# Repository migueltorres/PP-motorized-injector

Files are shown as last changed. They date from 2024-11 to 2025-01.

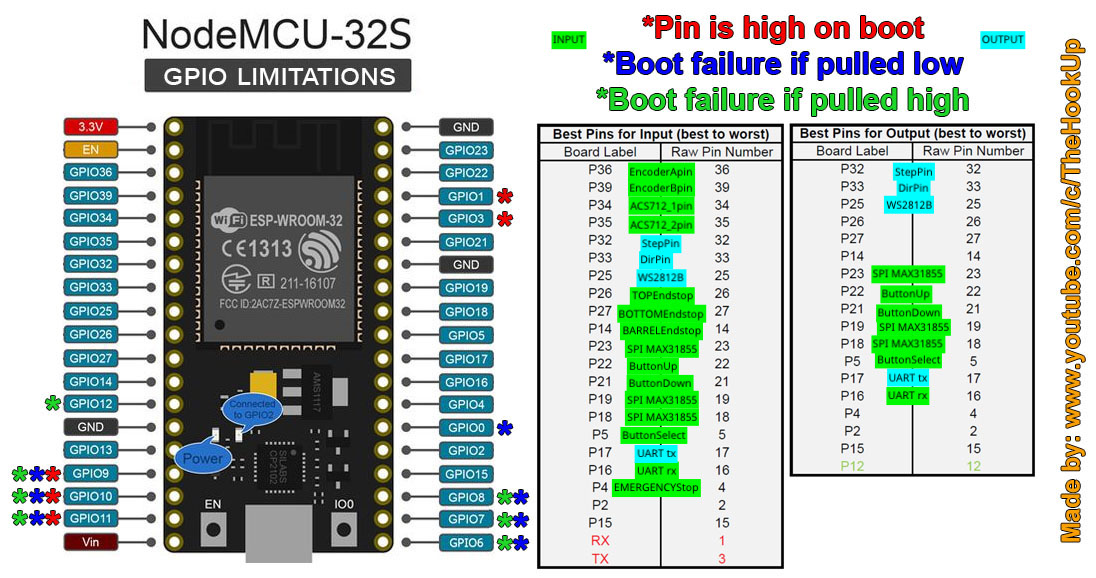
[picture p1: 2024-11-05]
GPIO_Limitations_ESP32_NodeMCU.jpg

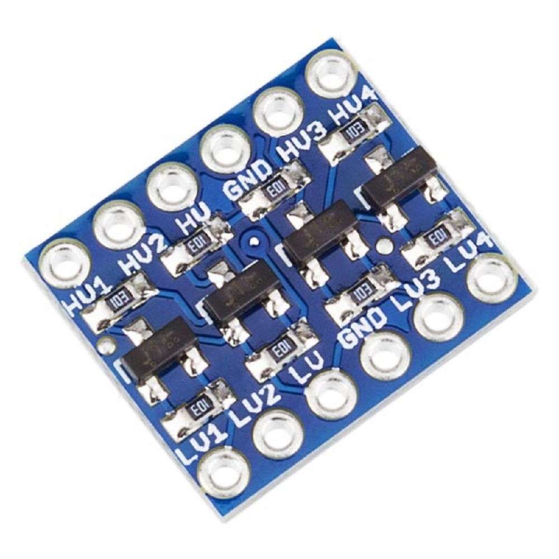
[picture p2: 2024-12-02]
4 channel bidirectional LLC.jpg

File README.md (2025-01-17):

# PP-motorized-injector
Motorized plastic injector using Arduino code to be open sourced with Precious Plastic initiative once working!

I create this (1st time on Github!) repo as I would like help in getting this finished and resolving issues that I am having (please excuse the extension of the descripcion, I am not known for my ability to summerize!):

I am making a PP influenced style injector, but controlled with Arduino to be able to send a Nema 34 160mm with Encoder, with 1:20 reduction to a 26mm ID / 50cm stroke injection barrel with control enough to be able to inject up to a 1/10th of a cm3 of plastic (more or less, the actual system is capable of even btter precision, but plastic is a dynamic fluid so don't expect the practice to reflect the theory 100%).. this need came about because the manual arbour version I made is so powerful that it injects great into large thick 3D moulds, but is difficult to fill smaller 2D moulds made from 8mm sandwich (originally these were a good format for the first lever-operated PP injector), as it is too easy to overfill and get flash, and then is very difficult to open the 2D mould and the part is ruined,.. and the smaller the part to inject, the more difficult it is to "feel" when it is full and to tehn over-fill - this machine should be able to calibrate to each mould the exact amount and speed of injection to get a perfect fill each time 🤞

I have done the mechanical design (still open to a couple of last minute choices about things like how to detect the presence of the mould/ nozzle blocking mech/ barrel blocking mech, etc) and believe it to be quite solid, as I have designed a few machines myself (https://bazar.preciousplastic.com/andys-recycling-machines/), including an arbour injector before the PP version came out.. I had asked for help documenting this to open source the design as this is a weak point for me, but didn't get much response 🤷, hopefully this time can get the help I need on the software side.. this is supposed to be open sourced as well..  

the machine for me should be able to inject into any type of mould, up to a maximum size (the space under the nozzle), and volumen (supposedly about 265cm3, pratice this will be about 200cm3 as the cold flakes have air), and different size moulds basically have a wooden block under them to make up the space needed so they are all at the same height, so to speak...  I generally inject max about 50-60cm3 with the manual machine, which has slightly smaller volumen (about 180cm3) and Refill after each injection

I have so far managed to integrate (inductive) endstops for top and bottom plunger movement, a barrel slip detection (my method on my manual injector of stopping heat from passing from the barrel to the rest of the machine, and so to be more efficient, is to clamp the barrel between 2 offset clamps, and the space is filled with cork sheet, works very well and the clamps do not get hot, but if the machine is incorrectly used and the plunger forced with nothing underneath the barrel, happens with the manual version too, then the barrel can clip in the clamp, changing the space below/calibration of the injection process), temp in nozzle detection (low temp, no move), and a 3 button LED backlit keypad at the height of the Nozzle to aid use of the machine when working down there (purging, zeroing for injection, injection itself, colores change and functions of each button)... all running on a ESP32 exclusively dedicated to running the motor, encoder, endstops, etc.

The other half of the electronics is a 2nd ESP32 Touchscreen display, connected to the motor ESP32 via UART, where can graphically add mould profiles, change parameters, store and load a list of moulds, and also graphically show the contents of the barrel; how much time each Refill has been in the barrel (during Production with the manual injector, I Refill after each Injection, but have to give time for each Refill Block to heat up as it travels down the barrel, so it has had time enough to reach melt temp before being injected, otherwie get a cold injection), once calibrated with a minTime can advise that the NextInjection amount and the RefillBlock at present about to be injected both pass in TimeHeated and amount to inject, to make sure that it will not be too cold.. everything is stored on this Display in flash, and only the NextInjection parameters are sent to the motor ESP32 via UART...  these are mould variables that change with each mould, there are also a load more common machine variables that are changeable from the display, like offsets from endstops, speeds and amounts of a compression function with auto-detection of max compression (the Nema will skip, the Encoder Compare function will notice this and reduce/stop compression), which once set up will rarely have to be changed/tuned

So far I have checked that each electronic component works with simple separate test sketches directly to the motor ESP.. the Display ESP I am still in the GUI design stage, using EEZ Studio (first time too, so learning curve 😜), but eventually will have to be connected, but until this 2nd stage is done, the same serial info should be able to be sent via Serial to change mould parameters, then all workings of the machine, following a State Machine programming style, will be possible from the 3 keypad control, as each State will give different options to the buttons to proceed or go back to other States as needed...

Here in this repo I have uploaded all notes, design considerations, and so far a few captures of the machine, and my next steps I hope to generate interest on the Discord server (which also rarely use😬).. I am 52 years old, completely self-learnt in all I have ever been interested in since I left home at 15 years old, so am very aware that what I do know is out-weighed by what I don't know in most of what I am learnt in life.. I am level 1 autistic, but intelligent enough to have masked most of my life until I auto-diagnosed about 6-7 years ago.. I personally do not like social networks, but aim to use Discord to learn from others and help try and get this machine up and running ASAP.. I have tried using ChatGPT with varing levels of success in getting every more complex sketches working (tab separated sketches seem to be my limit, can't seem to get more than the most basic ones working, when I understand that need to have a more modular approach with more tab separated header files, but here is were I have reached my limit!), but am also self-employed and PP here in Tenerife is not big enough to be able to dedicate all of my time, so I have other professional obligations that take time away from this proyect 🤷

I am not entirely sure about how to best proceed in questions of organisation via Discord, how to better use Github to centralize development of this proyect to benefit everyone in PP with this machine that I hope will open up easy injection to more people, but after seeing the latest video about PP problems and need to get to v5, I would like to make this public/ open source now (have been working over a year on this, on and off, and have the alpha built and waiting for a working sketch!)

I would need help integrating the State Machine I have designed into a working sketch, capable of responding to user button presses, and updating the ActualMould struct via Serial monitor to be able to change easier the MouldVariables (instead of having to reflash each time), and finalizing the way of detection for Compresion (nozzle blocking), Purging (barrel blocking but nozzle open, small forces to purge and check that plastic is ready for injection), and Injection (same, but now using the full force for the programed move to fill the mould).. am contemplating now placing Strain gauges below the injection platform (will see how much strain is registable as I made this area pretty solid to be able to resist the injection pressure, about 1500kgs estimated), and/or Time of Flight distance sensors next to the nozzle to "see" that there is something that should block the barrel, and considering intergrating a couple of current sensors in one of the Nema motor pairs (SimpleFOC style, but my driver (for this hardware version) is "step/dir", so cannot use SimpleFOC) to detect peaks (or lack of) motor current that may help me indicate build up of pressure that could show there is / is not something below the barrel..

Please revise the contents of the repo, advise on what else is needed here, info to understand better the machine/concept, etc, and if someone on Discord could help maybe make a thread/channel (I think it is called that..?) to organise and separate interest on advancing this proyect, that would be a big help too...

google sheets (exported from Numbers 😬) of BoM, calcs, and particularly the State Machine.. although can't remember when did this export..
https://docs.google.com/spreadsheets/d/1dTpOeWWeW3WKA8ZfMgRmvt531EJANU4MFCuCA3LTdP0/edit?usp=sharing

Thanks in advance, I feel I am a pretty good mechanic, my "tok" is getting machines to work (my manual machines work pretty well), but software, although have a few years unfer the belt am learning and can follow quite well in ArduinoIDE (PlatformIO is still a bit more of a mistery for me, hace tried and not got good results yet..), getting a more complex sketch like this to integrate is driving me a little crazy!

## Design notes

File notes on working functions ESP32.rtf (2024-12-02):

CHECK VOLTAGES THRU ACTUAL CIRCUIT, LLC, ETC
With ONLY step/dir connected from ESP32 to LLC, Dir(LLC)&Gnd (ESP32)=3,3v, but Dir(LLC)&Gnd (distribution board on backboard)=2v (or less?), and OUTPUT Dir was even less..?? 1.4-1.6v
alberto has given me 2 types of 4 channel LLC, one bidirectional, the other directional, so can try these, however will need 2x 5v and 3.3v wiring to power said LLCs, as need 2 of them…
** FIXED ** after Alberto recommended testing with a pot in series with first Dir signal and then Pulse signal, discovered that DRIVER inputs logic HIGH/LOW threshold is 1.3v, so NO LLC needed

Encoder 🟢

ESP32Encoder simpleEncoderDemo works fine, 1000PPR, via 3.3v, and pins spec in sketch.. in theory is via PCNT hardware counter… so do NOT need to update any variable, just when sending encoder position data, include a call to the counter for the actual value… this will almost always be in a static moment, so no need to call constantly, but during moves, can call each 0.5-1s..?
Encoder colours wires:
Red - vcc
White - gnd
Yellow - A+
Blue - B+
CHECKS! test how many encoder steps are 100% stroke, and use this variable (maxEncoderStepsPlunger) as a check before each InjectProcess starts, to make sure enough material is left in machine (before Purge show on screen, at PurgeZero also check and show Green or Red on screen if NextInject (+ 5%?) fits or not
CHECKS! during testing phases, include a Home function that does NOT automatically zero encoder, just reports EncoderPosition, to see if steps have been lost after a few hours use

FastAccelStepper 🟡
revise course https://valarsystems.com/blogs/val-2000/section-10-motor-setup as they use this library, ESP32, and show how to dedicate 1 Core of ESP32 to ONLY motor functions (core 0 is por default dedicated to wifi, and loop() is core 1, so as no wifi, use core 0), to guarantee uninterrupted function on this core, all other MCU loads cargo on other core, Encoder calls are off both cores and callable when required

include actual button/pot sketch to check functionality on ESP32…. does not respond to button presses, butpot values do work.. had also included both new inline ACS712 current sensors (with inline 10k resistor)..
separate and test each component with example sketches…
FIXED! it seems driver logic HIGH/LOW threshold is 1.3v, so NO LLC needed (tried 3 types LLC, all gave strange voltages at driver input on connecting to driver 🤷)
🟡 working 2 button sketch with fixed speed 50%, w/o LLC, motor moves smooth and with acceleration on button presses (Constant move).. to incorporate, distinct Programmed and Constant motor move functions

MotorFunction should be called from StateMachine, a) first taking the variables pertinent to that state and writing them to global standard MotorFunction variables, b) call MotorFunction to move motor with its standard variables, which should move as per the variables just updated

As will assign motor function as a task to Core 0, have to verify that calls from Core 1 loop() to this task/function on Core 0 will not need any special extra coding..?

WS2812B_tests 🟢
working test sketch to change colores of LEDs behind buttons
🔵 brightness of ALL LED’s change on button press, could be acceptable so user sees any brightness change is SOME button has been pressed
🟡 currentDuration tests not quite working, to change color of other LED’s after 1s, ok, but other LED does not change back to original color on release/!isPressed/changed/rose etc, not sure how to do this.. revise more examples..? adding another .update before second “if” does work, but not always..? also, is possibly adding more MCU time to check button, + debounce time..?
Also, in my use case, a button hold for currrentDuration will (in all cases?) make a change of State Machine, where a new set of color instructions will be generated anyway..? Will not need to change colores back (not working well), only reduce brightness (working fine) before next State will change colours anyway

Buttons_tests 🟢
Blue wire - down
Orange wire - up
orange/white wire - select
blue/white - gnd
respond perfectly well with Bounce2 library, can also measure a delay, si WB2812B tests above, check that all “long presses” will make a State Change anyway

Inductive endstops_tests
will be assigning as buttons with Bounce2 library as well, as they are basically buttons with HIGH/LOW logic…
Top & Bottom sensors are NO, 5v, go to LOW / GND on activation, so pins with pull-up to avoid floating
Clamp sensor is NC, 0v, goes HIGH / 5v on activation, so pin with pull-down to avoid floating
min working voltage 5v (do not work at 3.3v), and min signal returned 4.4 top and bottom, 4.7 clamp 🔽 step-down/ LLC

StateMachine - revise spreadsheet made to indicate all situations

INIT States, on power on
INIT_HEATING // temp of machine too low to allow movement
⁃ power on, temp < 170C,
⁃ NO MOTOR MOVE POSSIBLE,
⁃ button LED's RED solid

INIT_HOT_NOT_HOMED // temp above min, ready for movement
⁃ temp > 170C
⁃ button LED's YELLOW solid

INIT_HOMED_ENCODER_ZEROED // Homed for FIRST time after power on Zeros Encoder, ALL later homings do NOT reset Encoder
⁃ user has pressed for first time Home
⁃ motor moves to TopEndStop
⁃ Encoder is zeroed, InitEncoderZeroedFlag =1
⁃ Motor is only zeroed when about to do measured moves, will move to Refill position (set position from TopEndStop)

REFILL & COMPRESSION states
REFILL // position with plunger just above barrel opening, so user can load cold plastic into machine
⁃ motor moves to RefillOffsetPositiion
⁃ button LEDs GREEN/OFF/OFF (will return to Refill after NextInjection) or GREEN/BLUE/BLUE (will NOT return to Refill after NextInjection, EndOfDayFlag=1)
⁃ user can press both lower buttons to change bool EndOfDayFlag
⁃ user can press GREEN button to confirm loading complete & NozzleBlack is in place

COMPRESSION // motor will move down first at med speed, until ComparisonFunction goes above threshold, then will continue until 0 speed
⁃ button LED's RED (Cancel) / OFF (nothing) / RED FLASHING (Starting Compression), YELLOW FLASHING (ComparisonFunction active), GREEN SOLID (completed)
⁃ ComparisonFunction compares SentMotorSteps and RealEncoderSteps for every, ej. 20 (?) steps.. when detects ej 50% (?) loss (only 10 steps Real to Sent), reduces Speed to 50% (?) and continues again, until Speed is below minSpeedThresholdForCompression, and then exits function
⁃ InsufficientFillCheck - if Encoder steps show that < 80-90% (?) of stroke is full (motor moved > 20-10% (?) of StrokeLength before ComparisonFunction finishes, then advices user that another Refill is required and goes back to Refill

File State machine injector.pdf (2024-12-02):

ReadyToInject… buttons change to green top and bottom,
middle yellow
🟢 🟡 🟢 ☑ 🔼 🔽 ….

Power
on

INIT_HEATING

(external
control)

INIT_HOT_NOT
_HOMED

Temp

>170˚C

Request user to

HOME machine,
press 🟡 🔼 (2s)

INIT states, check temps ALWAYS, maybe give option to HOME at another point, to test if ENCODER has lost steps

Request user to
CONFIRM REFILL

barrel & position
barrel block

INSUFFICIENT_
FILL

COMPRESSION
detected less
than 80-90%
stroke is full?

REFILL & COMPRESSION states

!EndOfDayFlag
marked?
🌑 🌑 /🔵 🔵
Once machine is ready, hot, | and encoder Initially homed,
automatically goes to Refill | position and awaits user input

Once Compression is completed to sufficient level, and contents has been heated long enough (millis timer for each batch of Refilled plastic..?)

EndOfDayFlag

Injection Process

User positions mould | & blocks with platform
confirms Proceed with | double green button press
!EndOfDayFlag | ! EndOfDayFlag ?
MACHINE_EMPTY | Power off

INIT_HOMED_E
NCODER_ZER
OED

REFILL

Injection Process uses ActualInjectParams and CommonInjectParams, automatic, only CANCEL button or EMERGENCY STOP

INJECTION | HOLD_INJECTI
ON | RELEASE

COMPRESSIO
N

ProgrammedMotorMove function: parameters set from State to appropriate variable for appropriate move

ContinousMotorMove function: either from user button press (Purge), or internal command variable (Compress until motor & encoder desync steps)

🛑 🛑 🛑 ☑ 🔼 🔽
(no movement possible)

🟡 🟡 🟡 ☑ 🔼 🔽 (not homed yet, no refill/injection can be performed yet)

(🟢 🌑 🌑 ☑ 🔼 🔽 , waiting confirm Refill 🌑 🌑 !EndOfDayFlag 🔵 🔵 EndOfDayFlag cancel process ☑ 🛑 , middle off 🌑 🔼 , bottom button flashes red 🔽 🔴 , change to flashes yellow 🔽 🟡 , then green solid 🔽 🟢 , and complete

pressing both green buttons 🟢 🟢 ☑ 🔽 for 2s enters Injection Process

Press both bottom buttons 2s to change from black (!EndDay) to Blue (EndDay, no more Refills) or visa versa

User PURGES
plastic using UP /

DOWN buttons until
presses green to ZERO
PURGE_ZERO | ANTIDRIP

buttons change to green top, yellow bottom pair) 🟢 🟡 🟡 ☑ 🔼 🔽

green bottom pair 🟢 🟢 🔼 🔽 , press top 2s to cancel injection, bottom pair together 2s after positioning mould to start injection cycle

red top 🛑 ☑ (cancel
injection)go back to
ReadyToInject

pressing middle yellow button 🟡 🔼 can take back to Refill position (only way to get there once EndOfDayFlag is marked),

INJECT_TO_MOULD
red top (cancel), green bottom pair 🛑 🟢 🟢 ☑ 🔼 🔽

Communications via UART:
During certain States, the STM32 will be listening for commands to change to other States, or to change ActualInjectParams, or CommonInjectParams... this will only happen during States that make sense, for example ReadyToInject, Refill, NOT during motorMoves

however, the STM32 will be transmitting every 1s to the ESP32 the actual Encoder position, the actual Nozzle temp, which the ESP32 display will later show a graphic rep of the barrel and the contents as rectangles, with either timers in each rectangle, or colours to show plastic melt stage... other good Encoder transmission points may be at the end of Refill/ Compression functions, as these will be the boundary between rectangular blocks representing plastic Refills and therefore melt stages

Also, on listening and receiving Params changes (for Common or Actual InjectParams, the STM32, after updating these variables, will transmit back to the Display so they can be shown on screen and compared to requested data

STOPS:
EMERGENCY STOP, if pressed, immediate stop of actual function. if function is NOT plunger down move (compression or injection), then releasing E-STOP will return to same point, if IS down move, then will immediately de Release Function, and then enter Purge Function so plunger can be moved manually

Endstops:
TopEndStop: when plunger reaches Top of stroke, the barrel is supposedly empty, so simply stop any more movement up (possible send plunger to Refill position, as is a nearby offset, or only allow move down*)

BottomEndStop: the encoder data should update the total stroke of plunger and add the NextActualInjectionParams to the actual plunger position, and advise if the injection can be completed or not, but if the BES is triggered without this warning, stop motor move, only allow motor move up*

Barrel Endstop: if the barrel has been detected as having moved from its fixed place, then stop any movement/ injection and advise with error, only allow up move to allow release of pressure so clamp can be inspected without pressure*

* in theory, in none of these cases coincide with a user button config that ALLOWS any movement anyway, so possibly could include this movement ONLY... also, these types of endstops errors can easily be indicated by flashing LEDs red in order:- if top endstop is triggered, flash goes up, bottom, flashing goes down, if barrel, centre and exterior alternate 🤔

Buttons input and output:
Lower keypad consists of 3 buttons, select, up & down, with LEDs behind, that change use as per the State of the machine and user input required to operate. Simple direct connection GPIO with Pullup is considered enough.

Barrel & Nozzle block detection however is still complicated, as the force experimented in this area (full downforce from Nema motor via 20:1 reductor, about 1500kg estimated min) makes use of traditional mechanical endstops very difficult, and proximity sensores also may not fully verify that a decent blocking mech is in place, contacting both against the platform and against the barrel / nozzle edge (as per compression or purge) - it is considered a L-shaped 30x3mm profile with a blind end, as used with the manual machine, together with a toggle mech to be able to invert this L-profile as per need of the moment, manually... for an electronic check, this pivoting and inverting mech would have to be electrically isolated from the rest of the machine (which experiments continuity throughout the frame so is impossible to know when one part of the frame touches another, as there is already an alternative conductive route for the signal)

A plastic sleeve isolating the fixed side of a hinge and the mobile side that carries the L-profile mech could be a way to later connect said profile to a pin, but it would activate on touching EITHER barrel/nozzle OR platform base, when what is really needed is to assure the profile is correctly positioned between both sides, not just that is contacting either of them

For the moment, can only think about a Manually Display User Reminder to place the L-profile in the correctly orientated position as per the Purge or Compression function that need to be realised...

The same goes for the presence of the mould itself, complicated by the fact that each mould, although metallic, have a wooden base to supplement the height differences between moulds and the full injection space

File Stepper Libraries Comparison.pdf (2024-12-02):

### Feuille1

### Page 1

| Acceleration | Max steps/sec | Units | Non-blocking methods | ISR Note 1 | Notes
Stepper | No | ? | Step RPM | Blocking | No | Easy to use, only three methods
AccelStepper | Yes | 4000 Step | | Both | No
MobaTools | Yes (start/stop ramps) | ? | Step Degree (angle) | Non-blocking | No | The MobaTools are a compilation of classes that are useful in the model railway environment (but not only there). It can control servos and stepper motors (and other things).
FlexyStepper | Yes | 7000 | Step Revolution mm | Both | No
SpeedyStepper | Yes | 12500 | Step Revolution mm | Both | No | Similar to FlexyStepper but optimized for speed Cannot modify target position, speed or acceleration while motor is moving
FastAccelStepper | Yes | 50,000 to 200,000 depending on processor | Hz (steps/s) mHz (steps/1000s) microsec/step ticks | Both | Yes | Fully interrupt/task driven - no periodic function to be called from application loop Not all GPIO pins are allowed on ATmega architectures, see documentation
ESP_FlexyStepper | Yes | ? | Step Revolution mm | Both | Yes | This library is used to control one or more stepper motors with a ESP 32 module. Based on S.Reifels FlexyStepper library.
TeensyStep | Yes | 300,000 | Step | Both | Yes | Compatible with Teensy 3.x boards The library is able to handle synchronized as well as independent movement of up to 4 groups of up to 10 motors
TeensyStep4 | Yes | ? | Step | Both | Yes | Compatible with Teensy 4.x boards This library is very experimental and no support can be given at the moment

Note 1 : ISR (Interrupt Service Routine) is for librairies that can run as interrupt tasks without the need to use a periodic function in the main loop(). With this feature, one can do whatever is needed in the main loop() without having to worry about the impact on the motors.

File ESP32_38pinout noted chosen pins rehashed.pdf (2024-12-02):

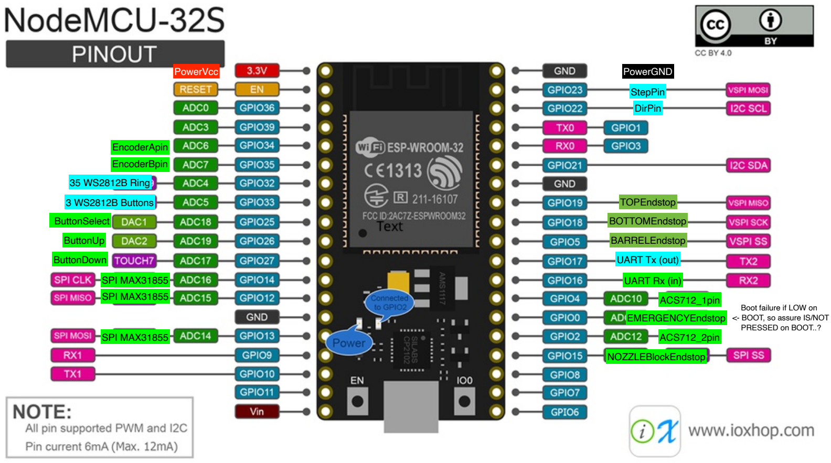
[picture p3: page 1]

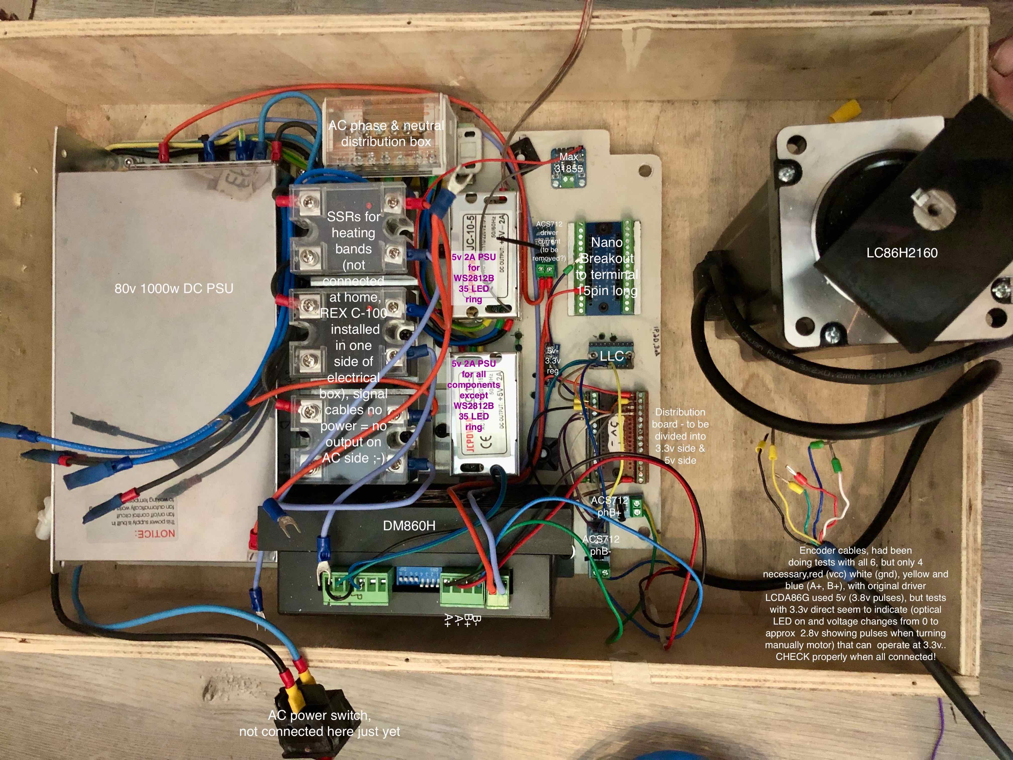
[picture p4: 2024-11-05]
electrical backboard layout.jpeg

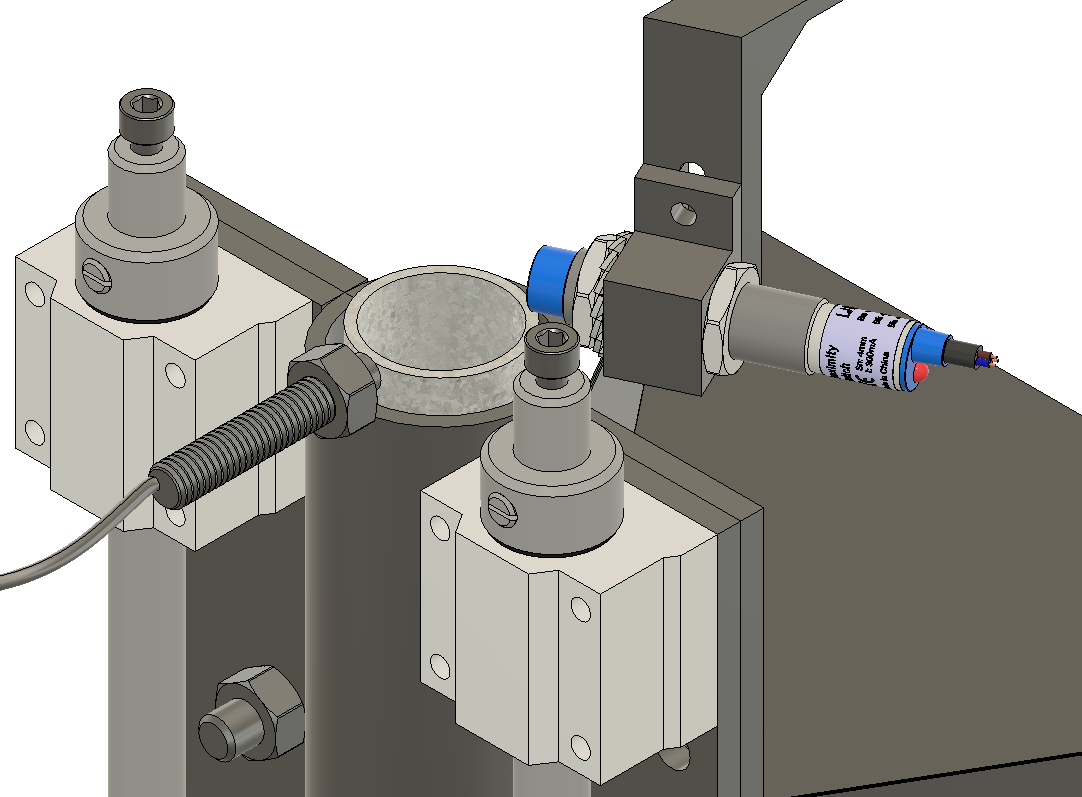
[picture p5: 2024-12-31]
fotos machine/clsoe up barrel slip, and bottom endstop.png

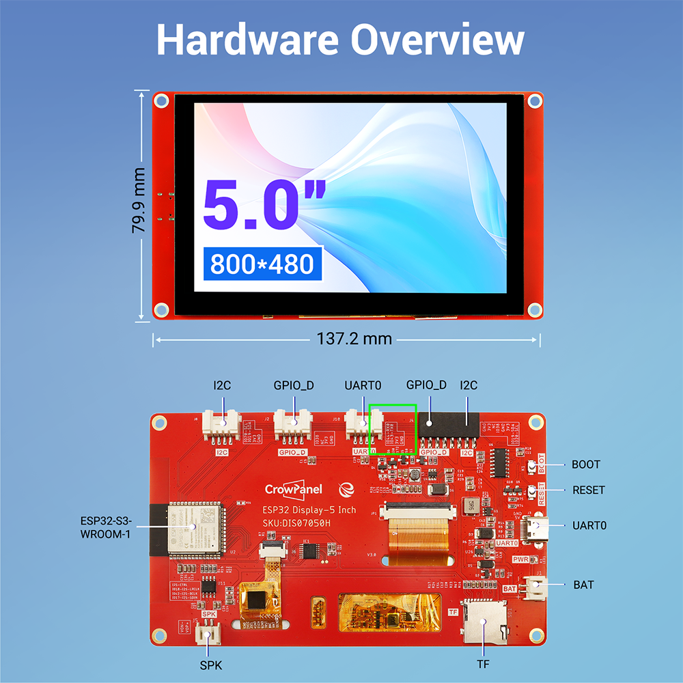
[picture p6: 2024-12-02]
elecrow 5 RGB 800x480 touch display/5-DIS07050H-SCH_PCB/dimension_size_of_ESP32_5inch_HMI_display.png

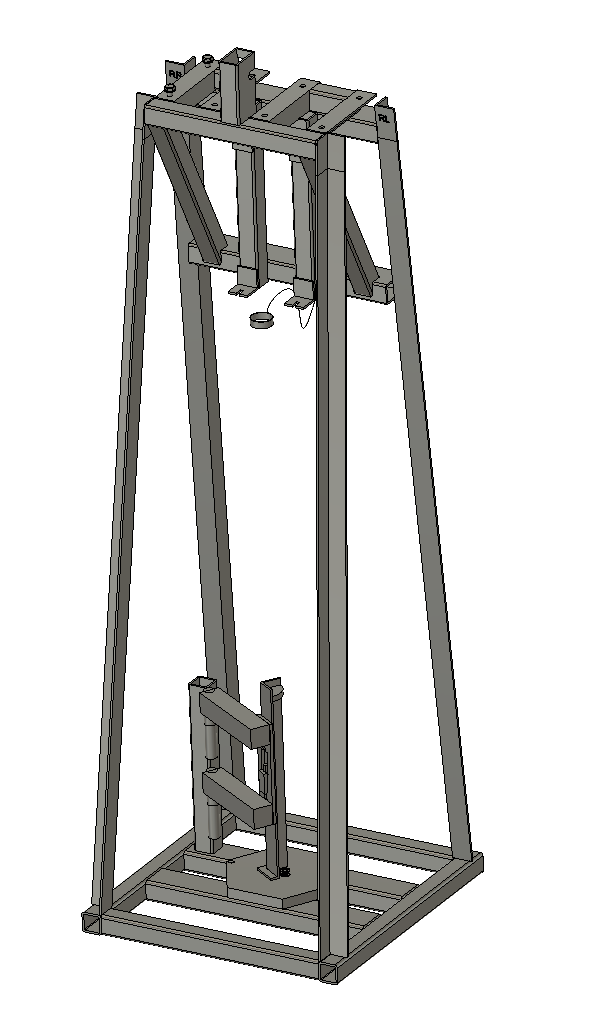
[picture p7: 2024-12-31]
fotos machine/frame only.png

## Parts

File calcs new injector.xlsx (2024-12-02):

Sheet: Calcs - Pump & injection pressu
Pump & injection pressures
Concepto |  |  | example
Dia embolo/cm | 2.600 |  | 4.500
Area embolo/cm2 | 5.309 |  | 15.904
Paso movimiento embolo/cm | 50.0 |  | 50.000
Volumen util/cm3 | 265.465 |  | 795.216
volume/s injection speed/cm3/s | 25
Tamaño orificio inyección/cm | 0.550 |  | 0.500
Area orificio/cm2 | 0.238 |  | 0.196
 |  | circumference | rev/full shot
Spur gear D1/mm | 60 | 188.4955592 | 2.652582385
radius/m | 0.030 |  | rev gear/25cm3 shot
power motor/Nm | 12.0 |  | 0.2498056796
power on spur gear/N | 400.000 |  | length of piston move/mm
power on spur gear/kg | 40.789 |  | 47.08726127
Nema 34 rpm | 900 | rps | 15
 |  |  | reduce from 15rps to 0.2498rps (shot 25cm3/s)
mechanical advantage gained from reducer/kg: | 2449.358 | ideal reducer by: (NOT actually used, just a nice calc!) | 60.05
Nm | 24020.000 |  | 🔼 after adding calcs for spur & shaft, this value seriously passes max values for both spur teeth and shaft torsion, so reduced majorly
pressure embolo en/ kg/cm2 | 461.334
punta embolo | 2449.358

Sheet: Calcs - Parts
Parts
part | code | price |  | value | unit
Nema34 closed loop stepper | https://robotdigg.com/product/1228/Two-phase-NEMA34-closed-loop-stepper-motor SS86P2156 | 120 | shaft 14mm 12Nm holding torque approx 900rpm=15rps | 12 | Nm
driver | https://www.robotdigg.com/product/1229 | included above..?
REDUCTOR RSTV050 TAMAÑO MOTOR 71 EJE DE ENTRADA 14 MM ratio i:20 would seem max for this setup | https://www.zuendo.com/corona-sin-fin/5166-reductor-rstv050-tamano-motor-71-eje-de-entrada-14-mm.html | 97.02 | ratio i:20 | 20 | :1 ratio
 |  |  | output after reductor | 240 | Nm
EJE SIMPLE DE SALIDA PARA REDUCTOR RSTV50 25 mm | https://www.zuendo.com/accesorios-para-reductores/3110-eje-simple-de-salida-para-reductor-todos-los-tamanos.html | 17.6 | diameter shaft | 0.025 | m
Spur gear mod 2.5, D1 60, hardened teeth | 22401-0125250024 | 34.32 | 60mm D1 14mm D2 | 0.03 | radius / m
 |  |  | power from spur gear onto gear rack | 8000 | N/radius spur
Gear rack 25 OD, mod 2.5 | 22425-025150X1000 | 130.67
Tube ID 26 OD 30 | 29050-0130X1000 | 20.64 | power from spur gear onto gear rack | 815.8 | kg
 |  |  | pressure/cm2 plunger PUMP PRESSURE | 153.7 | kg/cm2 / bar
 |  |  | pressure/cm2 nozzle hole INJECTION PRESSURE | 3433.634398 | kg/cm2 / bar
max rev Nema/ rps | 5 | rps | 25cm3 shot ratio to full shot | 10.61858317 | :1 ratio
steps/s | 2000 |  | rev/spur full shot | 2.652582385 | full = 50cm
rpm | 300 | rpm | time for full shot | 10.61032954 | s
rev Nema AFTER reductor /rps | 0.25 | rps | circumference spur | 18.84955592 | cm
rpm gear | 15 | rpm | steps / circ spur / cml | 8000 | 424.4131816
pulse/rev Nema // gear | 400 | 8000 | cm3/ cir spur | 100.08 | cm3
max pulse = rps / gear rps | 2000 | 0.25 | cm circ spur/s | 4.71238898 | cm
encoder pulses/ rev Nema | 2000
encoder pulses / max rps | 10000
25cm3 = cml / steps | 4.708726127 | 1998.445437 | cm3/ s | 25.01944716 | cm3
1cm3 = cml /steps | 0.188 | 79.93781747 | rev gear/25cm3 shot | 0.250 | rev
1cm lineal embolo = vol cm3 / steps | 5.309 | 424.4131816 | s/25cm3 shot | 0.999 | s
50cm linear plunger heated zone/ plastic full stroke = vol cm3/ steps | 265.4645792 | 21220.65908
67cm linear plunger full range move to topendstop 50cm stroke + 2cm cold + 6cm opening + 16cm clamp - 7cm plunger tip |  | 28435.68317 | 3819.718634 | <- RefillOffset steps= 16cm clamp - 7cm plunger tip x steps/cml sum of lengths to topendstop -> | 67
heated full stroke offset from topendstop,-> and from refill —> |  | 7215.024 | 3395.305

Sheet: Calcs - Volumes
Volumes
Injection Volumen = pi*radius^2*stroke | ej1, buscar volumen | ej2 buscar paso
EJEMPLOS de Calculos SOLO
Dia embolo / cm | 2.6 | 4.2
Paso embolo / cm | 50 | 10.82686688
Volumen inyectado /cm3 | 265.4645792 | 150

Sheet: Calcs - Rack & pinion, vertical
Rack & pinion, vertical
concept |  | Tangential force on rack | Torque on pinion |  | max calculated for heat hardened steel gear teeth
moved mass / kg | m | 4 |  |  | S=400Pa, w=25mm
gravitational constant / m/s2 | g | 9.81 |  |  | mod 2.5, 60mm Dp
coefficient of friction / u | u | -
maximum acceleration / m/s2 | a | 0.25 |  | max load N | 8225
pressing Force due to application / N | Fe | 8000 |  |  | with 50:1 reduction, about 1/2 the expected 😬
 |  |  |  |  | with 20:1 reduction, about 3% SF over the expected 🧐😰
Force on Rack / N | Fr | 8040.24
Torque on pinion / Nm |  |  | 241.2072
 |  |  |  |  | https://www.engineersedge.com/calculators/gear-tooth-strength-calculator.htm

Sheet: Calcs - Shaft calcs on chosen o
Shaft calcs on chosen output shaft
Shear stress on solid shaft | t = Tr/J | for 25mm OD | angular deflection | a=L*T/(J*G) | for Iron 63 GaP Shear modulus
 | Mpa | 78.22783763 |  | degrees | 0.8708128448
shear stress / t | Pa | 78227837.63 | angular shaft deflection / a | radians | 0.01519855131
twisting moment / T | Nm | 240 | length of shaft / L | m | 0.153
radius from center to stressed surface / r | m | 0.0125 |  |  | 🔼 length of shaft “as-theoretical-held-at-1-end”, whilst in reality, the reductor holds along 93mm of total 153mm, so torsion possibly only on last 53mm? = 0.3 degrees 🧐
polar moment of inertia of area / J | m4 | 3.83495197e-08 | Shear modulus of rigidity / G | Pa | 63000000000
J = (pi*Dˆ4/32) |  | 3.83495197e-08 |  |  | 🔼 as per Zuendo, axle is Iron, not steel!

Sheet: Calcs - Shaft calcs on motor sh
Shaft calcs on motor shaft, 14mm
Shear stress on solid shaft | t = Tr/J | for 14mm OD | angular deflection | a=L*T/(J*G) | for steel 75 GaP Shear modulus
 | Mpa | 22.27241186 |  | degrees | 0.4788470367
shear stress / t | Pa | 22272411.86 | angular shaft deflection / a | radians | 0.008357457403
twisting moment / T | Nm | 12 | length of shaft / L | m | 0.197
radius from center to stressed surface / r | m | 0.007 | Shear modulus of rigidity / G | Pa | 75000000000
polar moment of inertia of area / J | m4 | 3.771481981e-09
J = (pi*Dˆ4/32) |  | 3.771481981e-09

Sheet: BoM - Plunger parts
Plunger parts
part | description | web | reference | price (sin IGIC) | price € (con IGIC) | units | subtotal
Nema34 closed loop stepper | shaft 14mm 12Nm holding torque approx 900rpm=15rps | https://robotdigg.com/product/1228/Two-phase-NEMA34-closed-loop-stepper-motor SS86P2156 | CL86H2156 | $75.00 | €76.25 | 1 | €76.25
driver |  | https://www.robotdigg.com/product/1285/DM542,-DM556-or-DM860H-stepper-motor-driver | DM860HJK | $29.00 | €29.48 | 1 | €29.48
 |  | https://www.robotdigg.com/product/976/80VDC-7.2A-DSP-Stepper-Motor-Driver |  | $42.00 | €42.70 |  | €0.00
PSU 80v DC for Nema |  | https://www.robotdigg.com/product/1564/60V-or-80V-DC-output-500W-or-1000W-power-supply | S-1000-80 | $80.00 | €81.34 | 1 | €81.34
REDUCTOR RSTV050 TAMAÑO MOTOR 71 EJE DE ENTRADA 14 MM ratio i:20 would seem max for this setup | ratio i:20 | https://www.zuendo.com/corona-sin-fin/5166-reductor-rstv050-tamano-motor-71-eje-de-entrada-14-mm.html | B14, i=20..? could go to i:30 if decide that Nema is not reaching top speed with actual i:20, but this means more torque, and certain mechanical calcs indicate overload of gear teeth or axle 😬 | €80.17 | €85.78 | 1 | €85.78
EJE SIMPLE DE SALIDA PARA REDUCTOR RSTV50 25 mm |  | https://www.zuendo.com/accesorios-para-reductores/3110-eje-simple-de-salida-para-reductor-todos-los-tamanos.html | RSTV050 | €17.60 | €18.83 | 1 | €18.83
Spur gear mod 2.5, D1 60, hardened teeth | 60mm D1 14mm D2, hollow out to 25mm, add keyhole | norelem.es | 22401-0125250024 | €34.48 | €36.89 | 1 | €36.89
Bearing opposing spur gear | 35-15-19 bearing to retain gear rack against spur gear, have to carve out 25mm radius on outer surface with radial! | https://www.123rodamiento.es/rodamiento-cojinete/rodamiento-rodillos/leva/natr15a | NATR15A | €11.74 | €12.57 | 1.00 | €12.57
Aro suplemento | Aro 12mm-15mm, 22.5mm long, to suplement M12 bolt which holds bearing! | https://www.123rodamiento.es/rodamiento-cojinete/rodamiento-agujas/aros-interiores/ir12-15-22.5 | IR12-15-22.5 | €5.11 | €5.46 | 1.00 | €5.46
Bearing opposing spur gear, alternative | 32-12-14 bearing alternative smaller, does not need aro suplemento | https://www.123rodamiento.es/rodamiento-cojinete/rodamiento-rodillos/leva/natv12-pp | NATV12-PP | €16.20 | €17.33 |  | €0.00
Gear rack 25 OD, mod 2.5 | 880mm, with 70mm bronze tip 26mm OD | norelem.es | 22425-025150X1000 | €135.11 | €144.57 | 1 | €144.57
Bronze plunger tip | 26mm OD, 70mm long, buy oversize and turn on lathe | Asencio y hijos, o Graubassas |  | €30.00 | €32.10 | 1 | €32.10
1” male-male union | end of barrel to nozzle tip, solder to barrel to avoid plastic leakage (repass interior barrel) | Bolsa de Aguas La Cuesta |  | 5 | €5.35 | 1 | €5.35
1” male plug | nozzle tip, turn 45˚ tip, perforate to 5.5mm, tap to M6 | Bolsa de Aguas La Cuesta |  | 5 | €5.35 | 1 | €5.35
 |  |  |  |  |  |  | €533.98

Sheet: BoM - T-mech parts (moving side
T-mech parts (moving side)
part | description | web | code variant | price (sin IGIC) | price € (con IGIC) | units | subtotal
Tube ID 26 OD 30 | 750mm, 530mm below 60mm opening (120˚) | norelem.es | 29050-0130X1000 | €24.54 | €26.26 | 1 | €26.26
12mm linear bearings | 4x 12mm linear blocks | https://robotdigg.com/product/417/SCS12UU-Linear-Block | SCS12UU | $2.00 | €2.03 | 4 | €8.13
12mm smooth bar | 2x 230mm, cut from one 500mm length | https://robotdigg.com/product/920/8mm,-10mm-or-12mm-linear-shaft-or-smooth-rod-in-lengths | SR12_500 | $2.90 | €2.95 | 1 | €2.95
springs | 2x 44mm long, 12.5mm ID, 25mm OD | norelem.es | 26000-2512044 | €5.72 | €6.12 | 2 | €12.24
shaft collars | 2x 12mm | norelem.es | 07800-301202 | €2.67 | €2.86 | 2 | €5.71
Ceramic wool insolation | 515mm long, + Kapton tape & cylindrical metal mesh cover | poligono el rosario |  | €20.00 | €21.40 | 1 | €21.40
Kapton tape | 200mm wide, overlapped | https://robotdigg.com/product/35/Kapton-Tape-5mm-to-300mm-width | KPTape-200mm | $16.00 | €16.27 | 1 | €16.27
Protection heated barrel, 515mm long, perforated mesh | 515mm long, 398mm OD, + 15mm tabs | cortes y pliegues |  | €30.00 | €32.10 | 1 | €32.10
Cork, 2mm or 4mm | clamp isolation material | leroy merlin |  |  | €0.00 |  | €0.00
 |  |  |  |  |  |  | €125.06

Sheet: BoM - Electrical parts
Electrical parts
part | description | web | code variant | price (sin IGIC) | price € (con IGIC) | units | subtotal
band heaters | 5x 3070 240w 1x 4040 210w total 1410w 2 zones: barrel 960w (4.35A) nozzle 450w (2.05A) | https://robotdigg.com/product/1810/Electric-Copper-or-Brass-Band-Heater-for-Extrusion-or-Injection | 3070-220V240W 4040-220V210W | $10.00 | €10.17 | 8 | €81.34
PID temp controller | 2x, barrel & nozzle zones | https://robotdigg.com/product/1801/Digital-Adjustable-PID-Temperature-Controller-Panel-Thermostat | REX-C100 | $10.00 | €10.17 | 2 | €20.33
SSR 25A | 3x SSR 1 for pairs, 1 for nozzle, 2 for barrel | https://robotdigg.com/product/1240/Single-phase-slim-solid-state-relay | S-SSR25A | $10.00 | €10.17 | 3 | €30.50
Thermocouple | 2 for PID temp controller, | https://robotdigg.com/product/58/K-type-Thermocouple-0-to-600C | KTC320 | $1.00 | €1.02 | 2 | €2.03
 | 1 + breakout board for Arduino, screwed into barrel collar for temp check before moving plunger | https://robotdigg.com/product/911/1.2-meters-screw-head-K-type-Thermocouple | M3KTC | $4.00 | €4.07 | 1 | €4.07
 | + breakout board for Arduino | https://robotdigg.com/product/1256/3D-Printer-thermocouple-or-thermo-sensor-Breakout-Board | MKS31855 | $6.00 | €6.10 | 1 | €6.10
Caja eléctrica con back board | 400x300 caja poliéster + fondo | Coelca | PIN-630318 PIN-161002 | €62.26 | €66.62 | 1 | €66.62
Prensaestopas | M20 x2 M16 x6 | Coelca | GEW-GW52044 GEW-GW52043 | €1.00 | €1.07 | 10 | €10.70
Repartidor bipolar |  |  | GEW-GW44691 | €15.25 | €16.32 | 1 | €16.32
cable 3G2.5 |  |  | 5551150 | €1.34 | €1.43 | 8 | €11.47
enchufe aérea 16A |  |  |  | €2.41 | €2.58 | 1 | €2.58
 |  |  |  |  |  |  | €252.06

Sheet: BoM - floor mount
floor mount
bottom laterales | 327 | 2 | 654
bottom en medio | 267 | 5 | 1335
rear verticales | 1136.5 | 2 | 2273
front verticales | 1151.9 | 2 | 2303.8 | (1147.8 with 82degree cuts at each end)
 |  |  | 4576.8
 | 2288.4 |  | 6565.8
1st cut both profiles @: | 2300 | 2 | 3700 | 2365
 |  | leaves
2nd cut all 4 profiles, 2 @: | 1140 | 1160 | x2
other 2@: | halfway, leaves | 1850 | x4

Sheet: BoM - Frame
Frame
part | description | web | code variant | price (sin IGIC) | price € (con IGIC) | units | subtotal
base square 30x30x3 | 6ml |  |  | 20 | 3.333333333
139.5 | reductor support profiles |  | 558 | 1.86 | €1.99 | 4
267 | top main support (& bottom!) |  | 801 | 2.67 | €2.86 | 3
296 | side diagonal supports |  | 592 | 1.973333333 | €2.11 | 2
270.5 | t-mech support profiles |  | 541 | 1.803333333 | €1.93 | 2
 |  |  | 2492 | 8.306666667 | €8.89 | 1 | €8.89
rect 50x30x3 | 6ml |  |  | 35 | 5.833333333
110 | bearing housing |  | 110 | 0.6416666667 | €0.69 | 1
340 | centrales plataforma |  | 680 | 3.966666667 | €4.24 | 2
 |  |  |  |  | €4.93 | 1 | €4.93
L-angle 30x3 | 6ml |  | 2.833333333 | 17 | 2.833333333
30mm | t-mech shafts supports |  |  |  |  | 4
floor mount 40x40cm 30x30x3 | al final usé angels L, a ver como van!
400 | bottom stand outer laterals |  | 800 | 2.666666667 | €2.85 | 2
340 | bottom stand outer struts |  | 680 | 2.266666667 | €2.43 | 2
1136 | back verticals |  | 2272 | 7.573333333 | €8.10 | 2
1148 | front diagonals |  | 2296 | 7.653333333 | €8.19 | 2
 |  |  |  |  | €21.57 | 1 | €21.57
plataforma giratoria 150x150x10 |  | corona | approx | 25 |  | 1
tuerca M36
tornillo cabeza hex M36 x40mm
wall mount for 300mm moulds 50x30x3
267mm | spacer profiles |  |  |  |  | 2
wall mount L-angle 30x3
30mm | wall mount angles |  |  |  |  | 7
 |  |  |  |  |  |  | €35.39

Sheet: BoM - Screws
Screws
part | description | web | code variant | price (sin IGIC) | price € (con IGIC) | units | subtotal
M4 countersunk allen 25mm | linear bearings to rear clamp | toycasa |  |  | €0.00 | 16 | €0.00
M5 20mm allen head + washers | linear shafts fixation to frame | toycasa |  |  | €0.00 | 4 | €0.00
M8 20mm + washers + nuts welded to rear clamp (to avoid crashing with linear shaft) | clamps for barrel with cork in between | toycasa |  |  | €0.00 | 6 | €0.00
M12 50mm partial thread, 20mm thread, + 4 wide washers, + 1 locknut | Bearing against plunger, IMPORTANT 30mm NO THREAD, can get a longer partial threaded screw and cut shorter | toycasa |  |  | €0.00 | 1 | €0.00
M8 20-25mm 10.9, + washers & locknut | Reductor to frame - will have to make a util to hold nut at end of 140mm interior profile! | toycasa |  |  | €0.00 | 4 | €0.00
M8 90mm partial thread 10.9 | Plunger tip to plunger, empty 13mm ID x 8.5mm cavity, and all thru 8mm hole in tip, and 30-32mm deep 8mm hole in rack | toycasa |  |  | €0.00 |  | €0.00
 |  |  |  |  |  |  | €0.00

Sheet: BoM - Electronic parts
Electronic parts
part | description | web | code variant | price (sin IGIC) | price € (con IGIC) | units | subtotal
PSU Arduino 5v | power supply, regulated 5v, | https://robotdigg.com/product/1200/5V-2A-or-4A-Miniature-Switching-Power-Supply | PS5V4A | $3.20 | €3.42 | 1 | €3.42
PSU ESP32 3.3v | 3A, connect to ESP32 3.3v pin | Nalber |  | €11.00 | €11.77 | 1 | €11.77
Arduino ESP32 |  | Miqueas |  | €11.00 | €11.77 | 1 | €11.77
ESP32 breakout terminals |  | Temu |  | €4.00 | €4.28 | 1 | €4.28
TFT display | To show info about pots, sensors, actions, etc | Miqueas |  |  | €0.00 |  | €0.00
3 buttons Omron 12x12 | To adjust variables and initiate actions | Miqueas |  | €0.16 | €0.17 | 3 | €0.51
3 LEDs WS2812B | light buttons | Miqueas |  | 0.32 | €0.34 | 3 | €1.03
35 LED ring for nozzle lighting |  | Miqueas / Temu |  | 18.5 | €19.80 | 1 | €19.80
ESP32-S3 with 5” touchscreen |  | https://www.elecrow.com/esp32-display-5-inch-hmi-display-rgb-tft-lcd-touch-screen-support-lvgl.html |  | $27.13 | €27.58 | 1 | €27.58
Thermocouple | 1 + breakout board for Arduino, screwed into barrel collar for temp check before moving plunger | https://robotdigg.com/product/911/1.2-meters-screw-head-K-type-Thermocouple | M3KTC | $4.00 | €4.07 | 1 | €4.07
+ breakout board | + breakout board for Arduino | https://robotdigg.com/product/1256/3D-Printer-thermocouple-or-thermo-sensor-Breakout-Board | MKS31855 | $6.00 | €6.10 | 1 | €6.10
sensor inductivo 4mm dista | detection of plunger top & bottom end stop | https://electronicaelfaro.com/index.php?route=product/product&product_id=47599&search=1631 | LJ12A3-4-Z/BX |  | €7.95 | 2 | €15.90
sensor inductivo 2mm dista | detection barrel move |  |  |  | €0.00 |  | €0.00
 |  |  |  |  | €0.00 |  | €0.00
 |  |  |  |  |  |  | €90.33

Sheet: BoM - Mano de obra y consumible
Mano de obra y consumibles
concepto | cost | units | subtotal
USD/€ | €0.95
horas apuntadas | 20 | 59.5 | 1190
horas soldando |  |  | 0
hilo soldar | 35 | 1 | 35
electricidad |  |  | 0
transporte y despacho RobotDigg | 260 | 1 | 260
transporte y despacho Norelem | 100 | 1 | 100
Transporte y despacho Zuendo | 37.5 | 1 | 37.5
Transporte y despacho 123Rodamientos |  | 1 | 0
Transporte y despacho Elcrow |  | 1 | 0
 |  |  | 1622.5

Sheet: BoM - Totales
Totales
Table | Subtotal
Plunger parts | €533.98
T-mech parts (moving side) | €125.06
Electrical parts | €252.06
Frame | €35.39
Screws | €0.00
Electronic parts | €90.33
Mano de obra y consumibles | 1622.5
total cost, no margen (only MO) | 2659.317197

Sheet: Machine controls - Table 1
Table 1
Control | reason | how?
4x20 screen | show info about machine, temp, %amps to motor (pressure), amount to move next injection,
ESP32 | MCU to control everything
Speed of motor / plunger descent | faster filling better? | Pot1 to arduino variable
Force of motor /plunger | more pressure assures filling? | Pot2 to arduino variable
Time of movement | how long to descend plunger for…?
OR
Amount of movement | how MUCH to descend plunger… exact amount of plastic to fill! | Pot3 to arduino variable
Purge | make sure before injection that plastic in nozzle is not cold, but hot and fresh | Button or pot? | ex: press button, purge slowly, release button marks 0 for next injection, but if backing up is needed (to avoid dripping, sucks a small amount per sec back up), this is included in 0..?
Back movement after purging | exactly how much back movement after purge is needed, is this a variable depending on type & temp of plastic, so needs pot, or can be programmed in..? | Pot4 first, program later..?
holding pressure after the injection | after injection, pressure must be maintained 2-15s to avoid sink marks, depending on wall thickness/ part design | pot5, or possible programmed % time depending on temp and amount injected..?
Heat check | CANNOT move plunger when cold | Thermocouple with daughter board to Arduino, if TEMP=LOW, DO NOT MOVE
Barrel position check | if barrel slides down, moulds will no longer fit underneath nozzle with pre-made-for-each-mould shims | End stop against top end of barrel..? If barrel moves down, end stop becomes empty (NC to HIGH?)
Mould presence check | Make sure mould is present before injecting | End stop? | Do we need to assure exact lining..? All moulds are different, cannot assure via end stop only that this particular mould is correctly lined up..
INJECT! | All is in order, proceed with automatic injection | Button | On pressing INJECT, code should copy all variables to int fixed vales, to avoid any changes in variables during injection may otherwise cause issues..?

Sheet: Machine controls - Table 2
Table 2
Control | reason | how?
5” or 7” 800x480 ESP32-S3 touchscreen | show info about machine, temp, %amps to motor (pressure), amount to move next injection, |  | https://www.elecrow.com/display/esp-hmi-display.html
Speed of motor / plunger descent | faster filling better? | Touch control1
Force of motor /plunger | more pressure assures filling? | Touch control2
Time of movement | how long to descend plunger for…?
OR
Amount of movement | how MUCH to descend plunger… exact amount of plastic to fill! | Touch control3
Purge | make sure before injection that plastic in nozzle is not cold, but hot and fresh | Button or touch control? | ex: press button, purge slowly, release button marks 0 for next injection, but if backing up is needed (to avoid dripping, sucks a small amount per sec back up), this is included in 0..?
Back movement after purging | exactly how much back movement after purge is needed, is this a variable depending on type & temp of plastic, so needs pot, or can be programmed in..? | Touch control4, can be hidden later
holding pressure after the injection | after injection, pressure must be maintained 2-15s to avoid sink marks, depending on wall thickness/ part design | touch control5, or possible programmed % time depending on temp and amount injected..?
Heat check | CANNOT move plunger when cold | Thermocouple with daughter board to Arduino, if TEMP=LOW, DO NOT MOVE
Barrel position check | if barrel slides down, moulds will no longer fit underneath nozzle with pre-made-for-each-mould shims | End stop against top end of barrel..? If barrel moves down, end stop becomes empty (NC to HIGH?)
Mould presence check | Make sure mould is present before injecting | End stop?
INJECT! | All is in order, proceed with automatic injection | Button

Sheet: Consumos electronica - 3.3v and
3.3v and 5v consumos PSU
item | 3.3v consumo mA | 5v consumo mA | signal to/from STM32? (LLC 3.3v - 5v, pins)
ESP32 | -240 | -160
Inductive LJ12A3-4-Z/BX |  | -300 | 1
Inductive LJ12A3-4-Z/BX |  | -300 | 1
FINDA inductive |  | -50 | 1
Step & pulse |  |  | 2
Encoder |  | ? | 2
AMS1117 buck down | 800 | -10 | 2
current sensor x2, phA & phB for inline sensing |  | -10 | 2
Max31855 thermocouple | -1.5 |  | 3
WS2812B LEDs 35 ring |  |  | 1
WS2812B LEDs 3 buttons |  | -180 | 1
WS2812B LEDs 35 ring |  | -2100 | 1
Elecrow 5” display |  | -2000 | 2
5v 7A PSU |  | 7000
extra mA… | 558.5 | 1890 | 16

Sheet: Consumos electronica - 3.3v, LL
3.3v, LLC, 5v power & signals
item | 3.3v power | 3.3v signals | 5v power | 5v LLC signals | Pins on ESP32
motor Step/Dir |  | 2, Step & Dir | Gnd |  | pin 23 & 22
Encoder (should be 5v, works with 3.3v🤷) | Vcc, Gnd | 2, A & B |  |  | pin 34 & 35
AMS1117 buck down 5v - 3.3v | Vcc, Gnd |  | Vcc, Gnd
ESP32 | Vcc, Gnd |  |  |  | 3V3, Gnd
USART3 to ESP32 (serial pass thru) |  | 2, TX, RX |  |  | pin 17 & 16
Button select | Gnd Shared via continuation of button itself | 1 Pullup |  |  | pin 25
Button up |  | 1 Pullup |  |  | pin 26
button down |  | 1 Pullup |  |  | pin 27
LLC | VccA |  | VccB, Gnd | 4
Inductive LJ12A3-4-Z/BX TopEndstop |  | 1 Pullup* | Vcc, Gnd Shared | -1 | pin 19
Inductive LJ12A3-4-Z/BX BottomEndstop |  | 1 Pullup* |  | -1 | pin 18
FINDA inductive BarrelEndstop |  | 1 Pulldown* |  | -1 | pin 5
NozzleBlockEndstop |  | 1 Pullup* or analog..? |  |  | (pin 15)
EmergencyEndstop |  | 1 Pullup* |  |  | pin 0 * boot failure if pulled LOW
current sensor, phA for inline sensing 1K resistor to analog |  | analog** | Vcc, Gnd Shared | 0 | (pin 4)
current sensor, phB for inline sensing |  | analog** |  | 0 | (pin 2)
Max31855 thermocouple | Vcc, Gnd | 3, MOSI, SCK, MISO |  |  | pin 13, 14, 12
WS2812B LEDs 3 buttons |  | timer..? | Vcc, Gnd |  | pin 33
WS2812B LEDs 35 ring, Vcc, Gnd direct to 2nd PSU |  | timer..? | Vcc, Gnd |  | pin 32
PSU 5v 7A |  |  | Vcc, Gnd
 | 3.3v distribution |  | 5v distribucion | LLC spare
vcc | 5 |  | 7 | 1
gnd | 5 |  | 8
Could divide distribution board (15 pins) in 3.3v side (7 entries) and
5v side (8 entries)
Power sharing only possible for similar components, thick enough to grimp (inductive)
or max 2 male dupont (ACS)
* check signal from inductive is NO (active LOW with pullup) or NC (active LOW with pulldown)
** not sure how to use yet, but although 5v, as are 20A sensor, and motor will not pull more than
7.2A, should not be a problem to use 3.3v analog, as voltage range should be well below 3.3v
(approx 1.8v).. HOWEVER, I think they use 2.5v offset to be able to show +ve & -ve current 🤦
so maybe need resistors to not burn ESP32 ADC input..?
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

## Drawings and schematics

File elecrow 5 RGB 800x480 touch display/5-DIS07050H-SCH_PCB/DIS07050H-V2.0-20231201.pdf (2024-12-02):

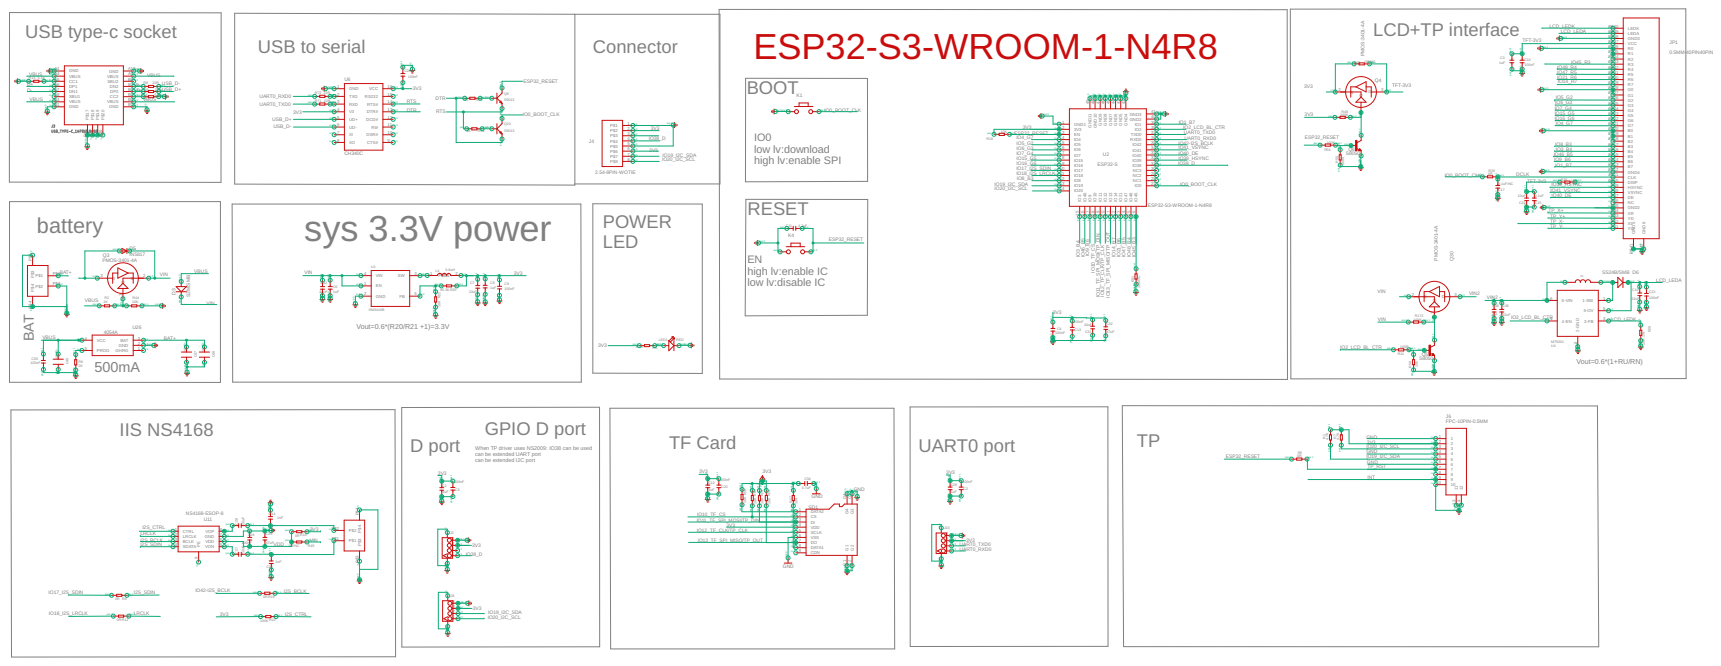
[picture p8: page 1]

high lv:enable SPI

sup 0
high lv:enable IC

low lv:disable IC

When TP driver uses NS2009: IO38 can be used
can be extended UART port can be extended I2C port

pas 1 pas 1 pas 1 pas 1 sup 0 sup 0

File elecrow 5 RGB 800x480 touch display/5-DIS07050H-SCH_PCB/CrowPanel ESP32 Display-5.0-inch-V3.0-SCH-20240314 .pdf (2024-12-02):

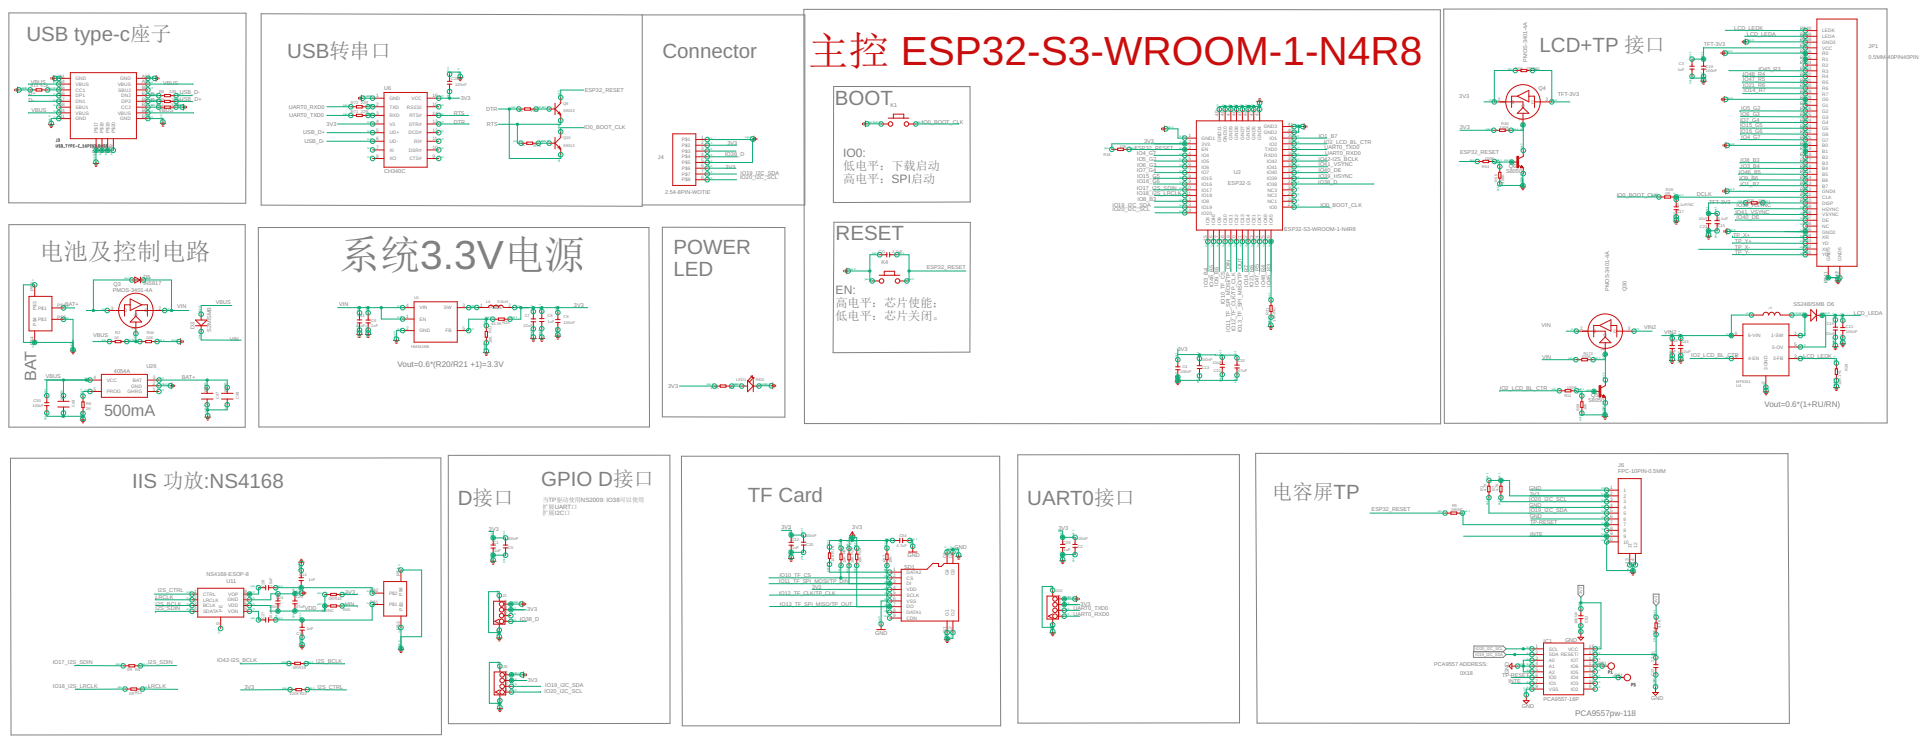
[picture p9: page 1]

pas 1 pas 1 pas 1 pas 1 sup 0 sup 0

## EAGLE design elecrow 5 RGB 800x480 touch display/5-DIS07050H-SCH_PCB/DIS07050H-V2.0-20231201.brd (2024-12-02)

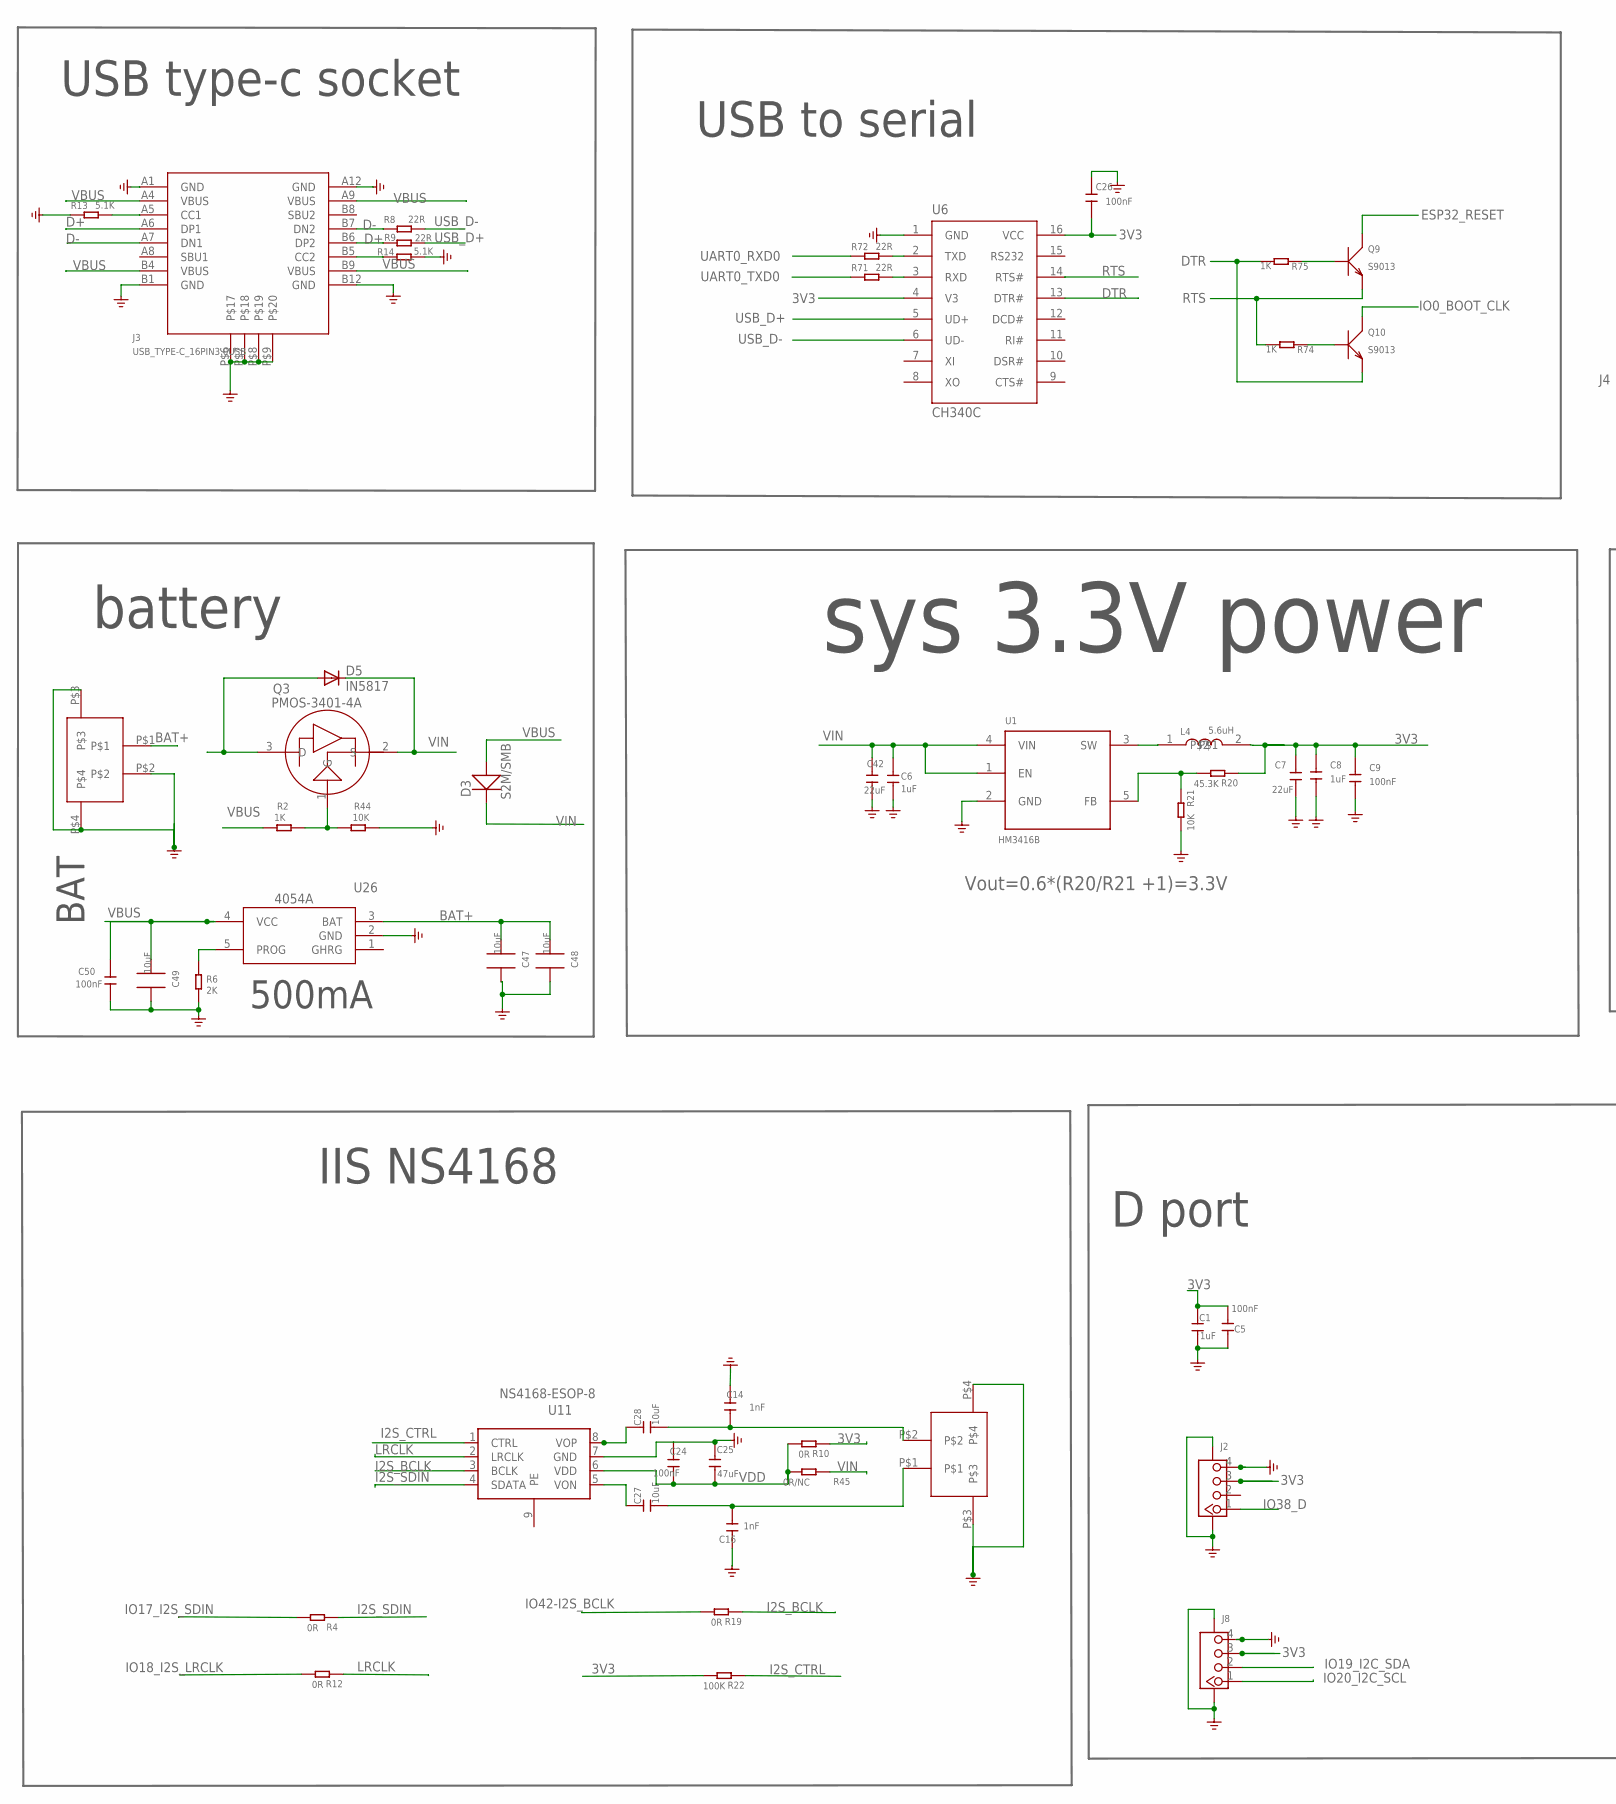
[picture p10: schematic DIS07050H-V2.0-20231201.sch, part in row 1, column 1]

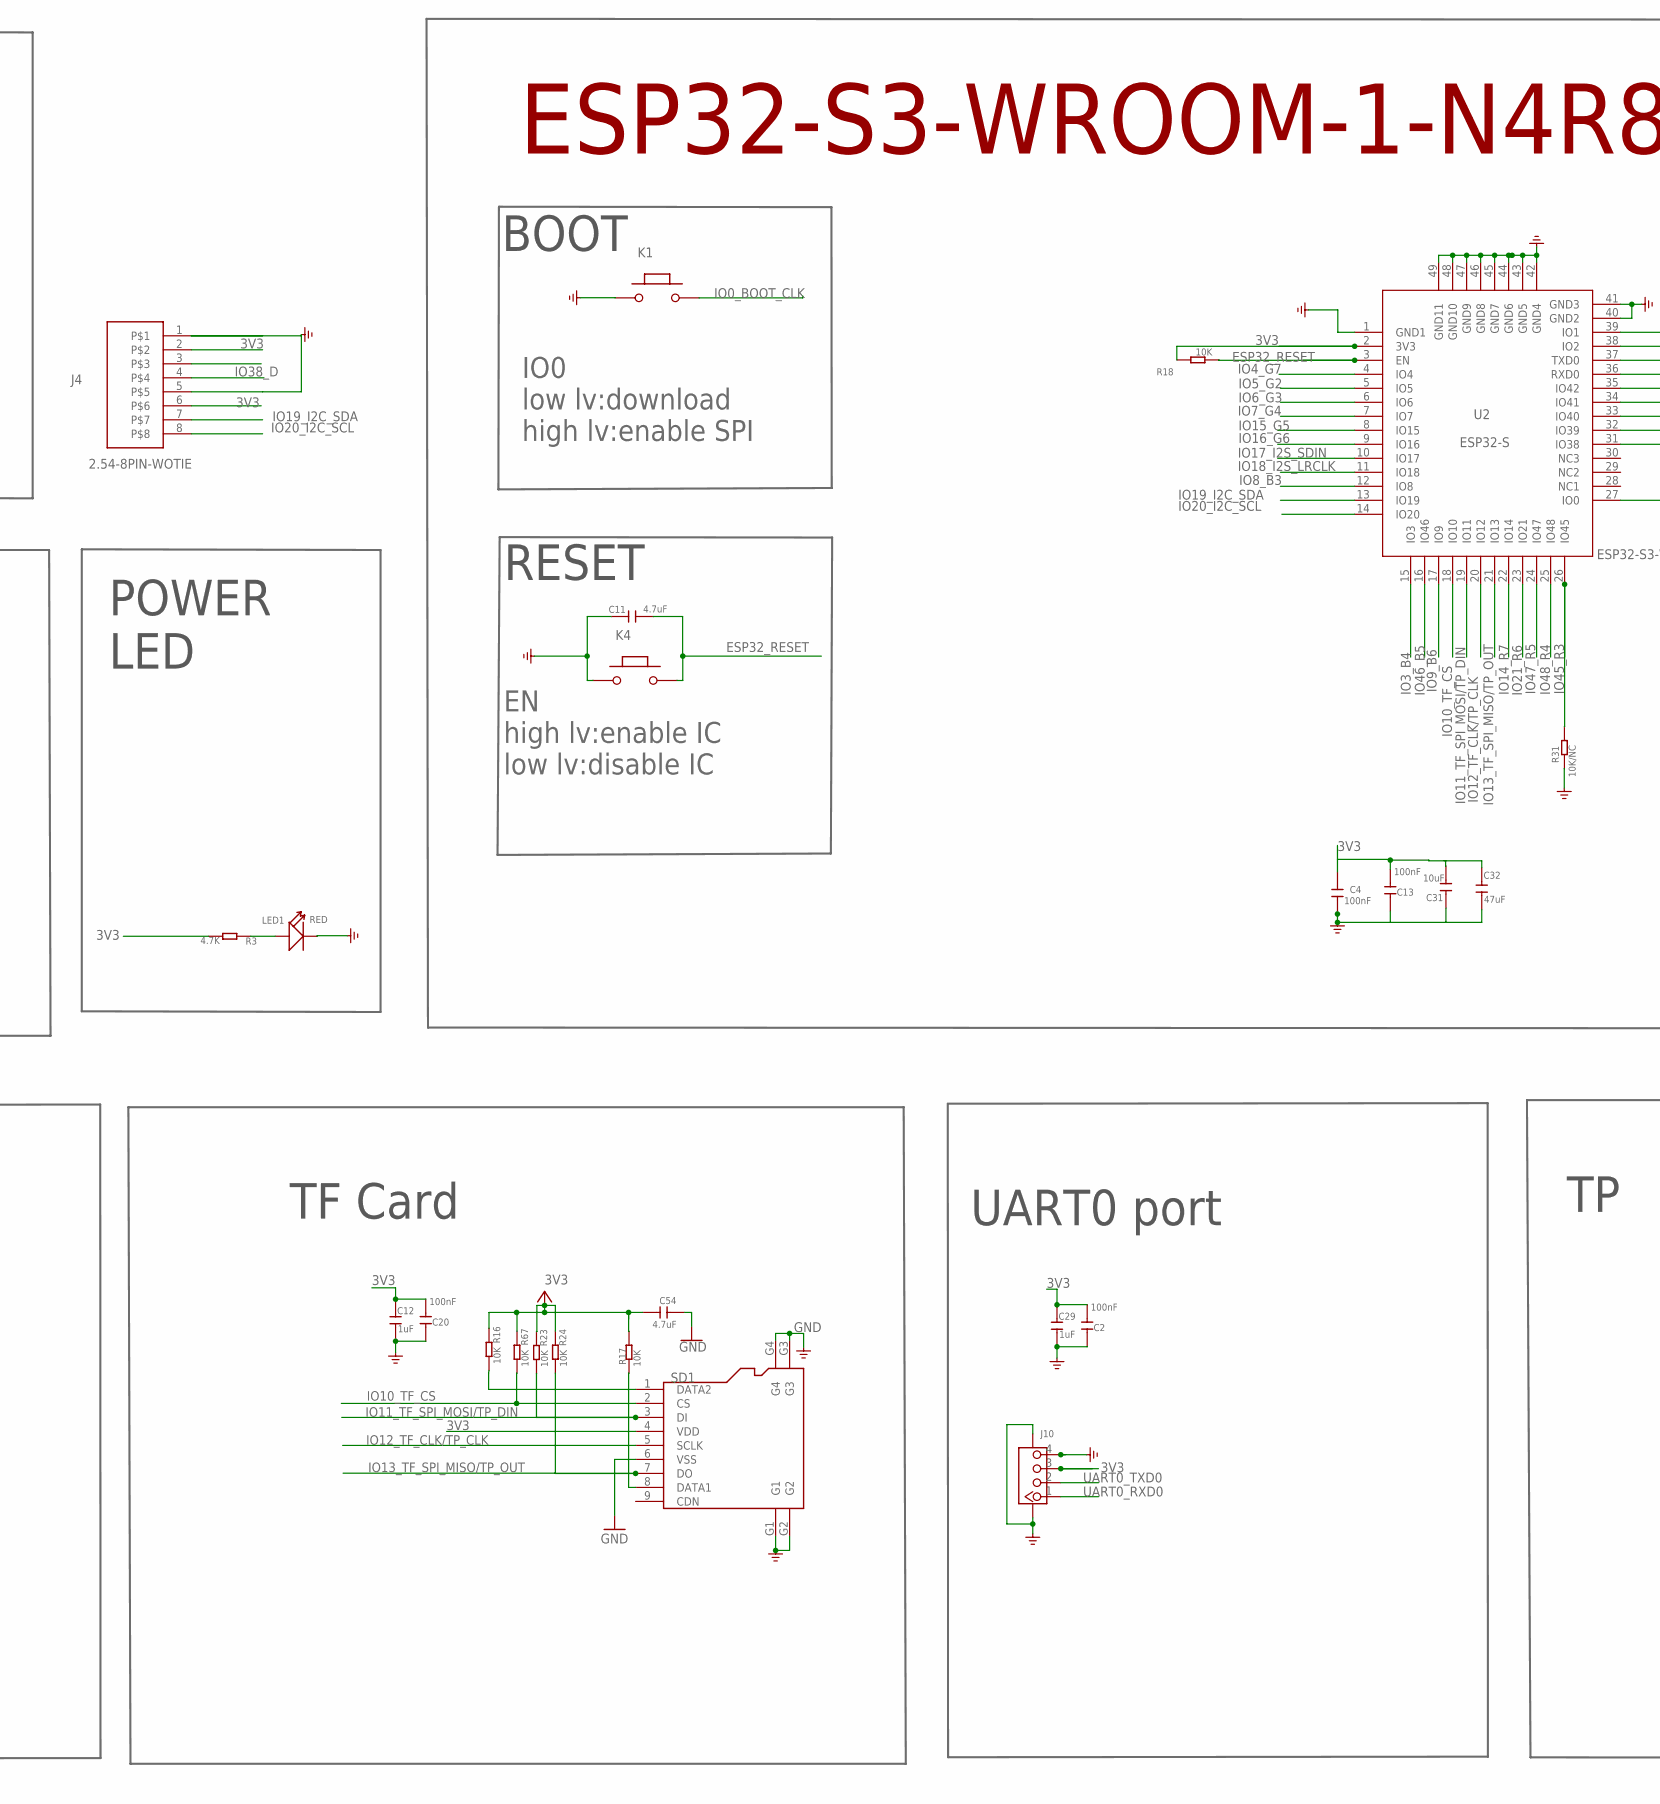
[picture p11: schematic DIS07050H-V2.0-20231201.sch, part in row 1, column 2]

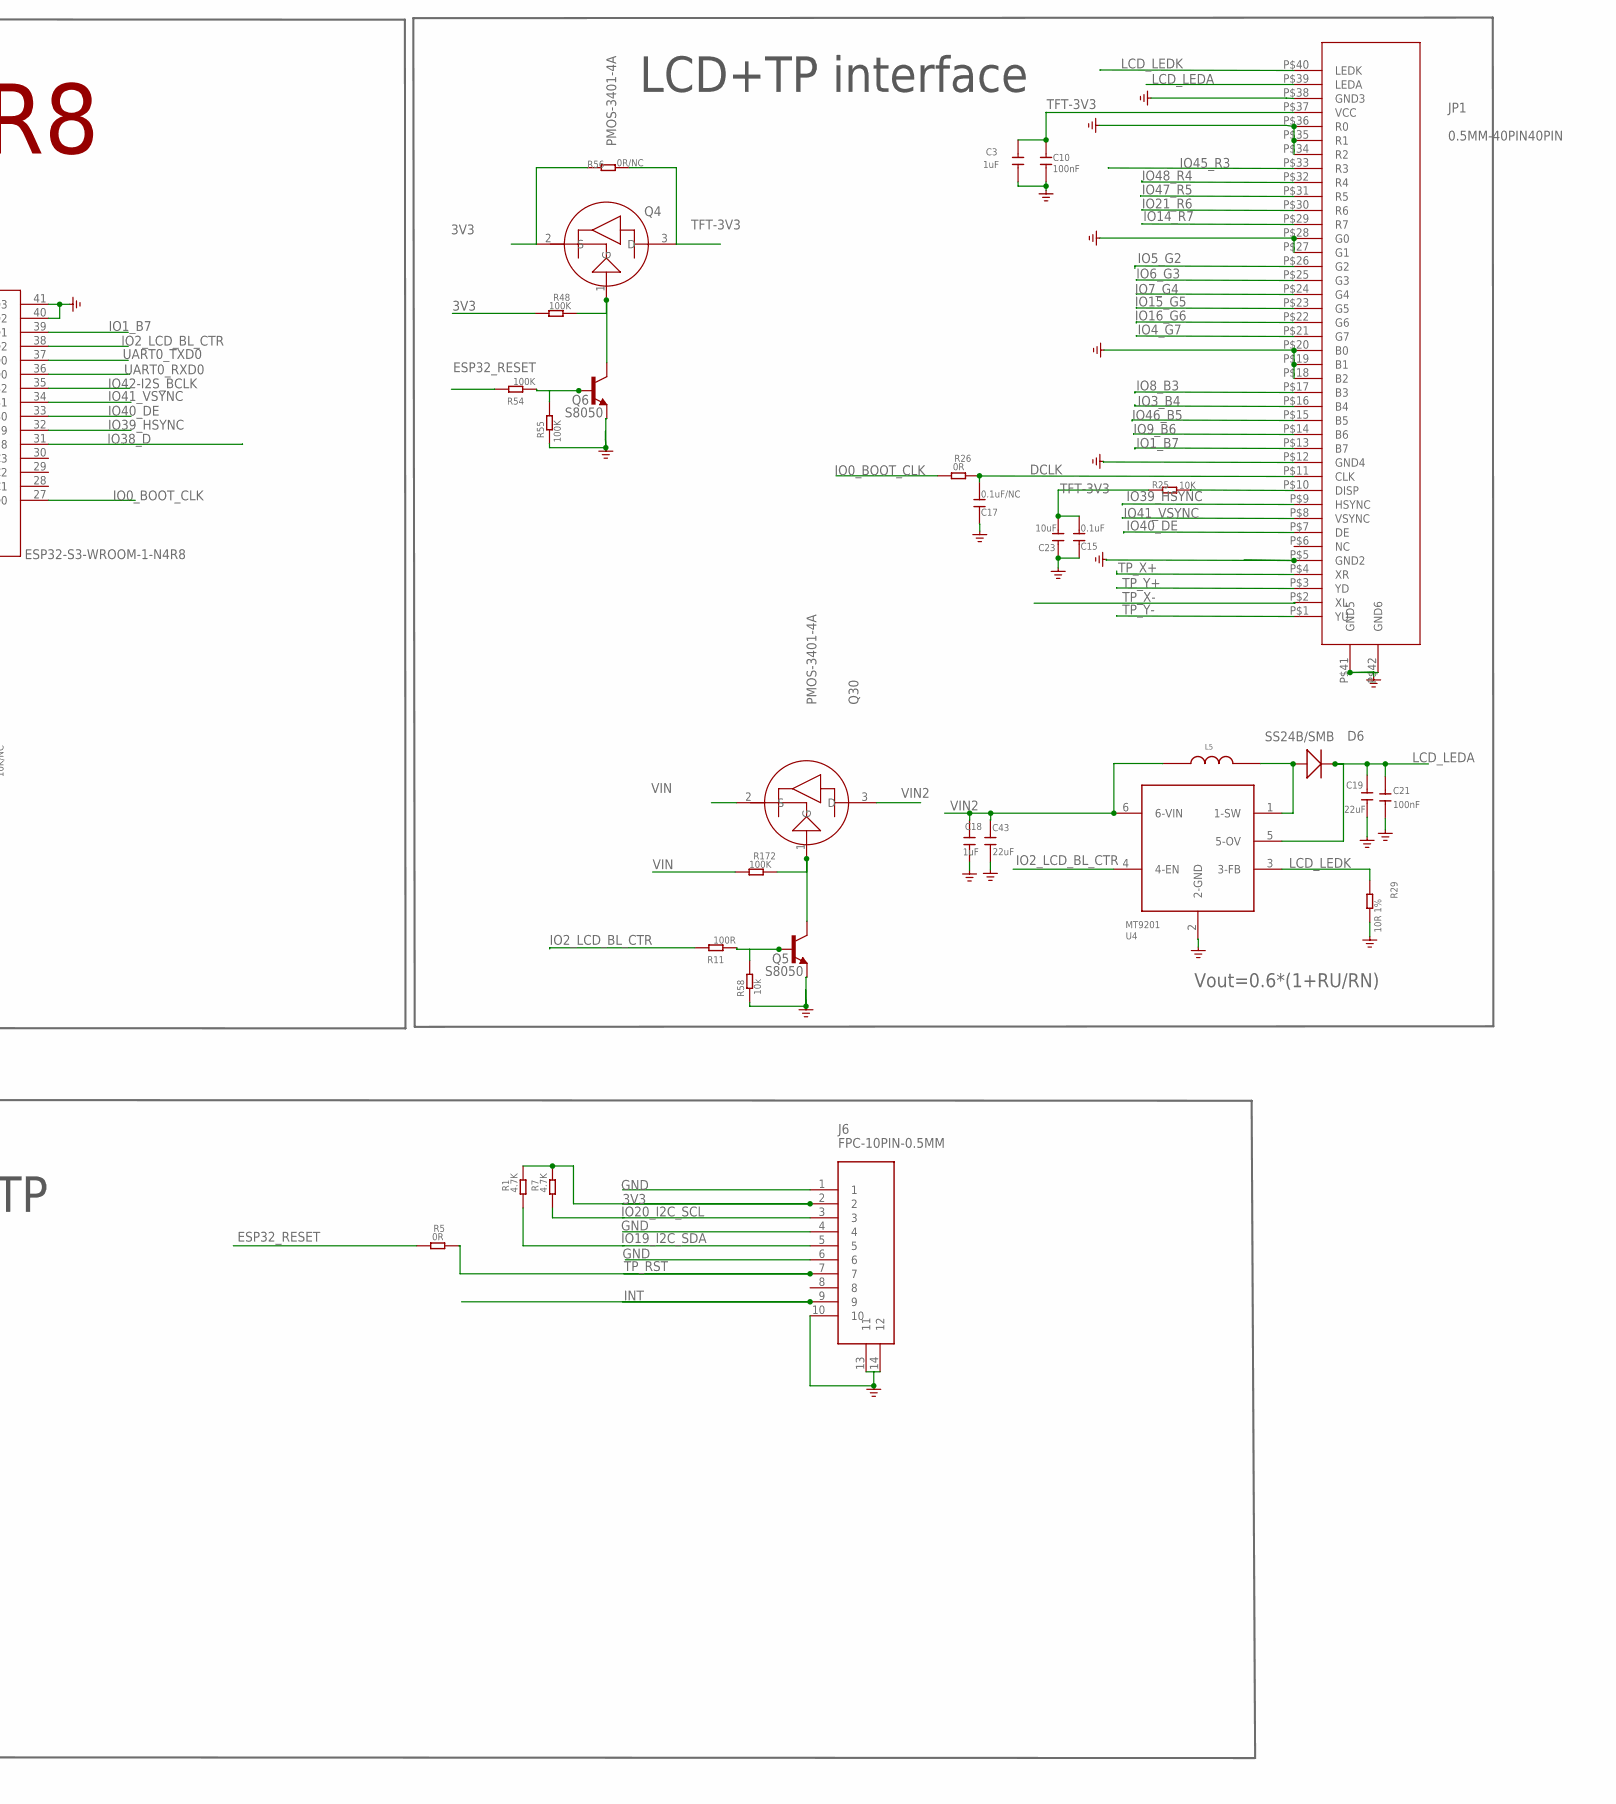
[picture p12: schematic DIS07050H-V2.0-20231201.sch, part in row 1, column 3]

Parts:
C1, C12, C29: 1uF; DISCRETE_C0603
C2, C4, C5, C10, C13, C20, C24, C50: 100nF; C0603
C3: 1uF; C0603
C6, C8, C18: 1uF; 0603
C7, C19, C42, C43: 22uF; 0805
C9, C21, C26: 100nF; 0603
C11: 4.7uF; 0603
C14, C16: 1nF; C0603
C15: 0.1uF; DISCRETE_C0603
C17: 0.1uF/NC; DISCRETE_C0603
C23, C27, C28, C31: 10uF; DISCRETE_C0603
C25, C32: 47uF; 0805
C47, C48, C49: 10uF; 0805_S
C54: 4.7uF; DISCRETE_C0603
D3: S2M/SMB; 214AB
D5: IN5817; DO-214AC
D6: SS24B/SMB; 214AB
J1, J5: PH2.0WT-2PIN
J2, J8, J10: CONNECTOR_TWIG-4P-2.0-SMD-FEMALE-REINFORCE90D; CONNECTOR_4P-SMD-2.0-90D
J3: USB_TYPE-C_16PIN3.0USB; KEVIN_3.0TYPEC-SMD
J4: 2.54-8PIN-WOTIE; 2.54-8P-WOTIE
J6: FPC-10PIN-0.5MM
JP1: 0.5MM-40PIN40PIN; 0.5MM*40P
K1, K4: BUTTON; 157SW
L4: 5.6uH; CD54_CD54
L5: CD32_6.8uH; CD32
LED1: RED; DISCRETE_LED-0603
Q3, Q4, Q30: PMOS-3401-4A; SOT-23
Q5, Q6: S8050; SPARKFUN_SOT23
Q9, Q10: S9013; SOT23@1
R1, R7: 4.7K; R0603
R2, R74, R75: 1K; DISCRETE_R0603
R3: 4.7K; DISCRETE_R0603
R4, R10, R12, R19: 0R; DISCRETE_R0603
R5, R26: 0R; R0603
R6: 2K; DISCRETE_R0603
R8, R9, R71, R72: 22R; DISCRETE_R0603
R11: 100R; R0603
R13, R14: 5.1K; DISCRETE_R0603
R16, R17, R18, R21, R23, R24, R25, R44, R67: 10K; DISCRETE_R0603
R20: 45.3K; DISCRETE_R0603
R22: 100K; DISCRETE_R0603
R29: 10R 1%; DISCRETE_R0603
R31: 10K/NC; R0603
R45, R56: 0R/NC; DISCRETE_R0603
R48, R54, R55, R172: 100K; R0603
R58: 10k; R0603
SD1: HOLDER-MICROSD-9P; 9P-SMD-W/-RING
U1: HM3416B; A_XBJ_SOT23-5
U2: ESP32-S; ESP32-S3
U4: MT9201; SOT23-6
U6: CH340C; SOP-16
U11: NS4168-ESOP-8
U26: 4054A; SOP23-5

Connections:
3V3: C1.2, C2.1, C4.2, C5.1, C7.2, C8.2, C9.2, C12.2, C13.1, C20.1, C26.1, C29.2, C31.2, C32.2, C54.2, J2.3, J4.2, J4.6, J6.2, J8.3, J10.3, L4.2, Q4.2 (S), R1.2, R3.2, R7.2, R10.1, R16.1, R17.1, R18.1, R20.1, R22.2, R23.1, R24.1, R48.1, R56.1, R67.1, SD1.4 (VDD), U2.2 (3V3), U6.4 (V3), U6.16 (VCC)
BAT+: C47.2, C48.2, D5.A, J1.P$1, Q3.3 (D), U26.3 (BAT)
D+: J3.A6 (DP1), J3.B6 (DP2), R9.1
D-: J3.A7 (DN1), J3.B7 (DN2), R8.1
DCLK: C17.2, JP1.P$11 (CLK), R26.2
DTR: Q10.2 (E), R75.2, U6.13 (DTR#)
ESP32_RESET: C11.1, K4.2, Q9.3 (C), R5.1, R18.2, R54.2, U2.3 (EN)
GND: C1.1, C2.2, C3.2, C4.1, C5.2, C6.1, C7.1, C8.1, C9.1, C10.1, C11.2, C12.1, C13.2, C14.2, C15.1, C16.2, C17.1, C18.1, C19.1, C20.2, C21.1, C23.1, C24.2, C25.2, C26.2, C29.1, C31.1, C32.1, C42.1, C43.1, C47.1, C48.1, C49.1, C50.2, C54.1, J1.P$2, J1.P$3, J1.P$4, J2.4, J2.SS1, J2.SS2, J3.A1 (GND), J3.A12 (GND), J3.B1 (GND), J3.B12 (GND), J3.P$6, J3.P$7, J3.P$8, J3.P$9, J4.1, J4.5, J5.P$3, J5.P$4, J6.1, J6.4, J6.6, J6.10, J6.13 (11), J6.14 (12), J8.4, J8.SS1, J8.SS2, J10.4, J10.SS1, J10.SS2, JP1.P$5 (GND2), JP1.P$12 (GND4), JP1.P$18 (B2), JP1.P$19 (B1), JP1.P$20 (B0), JP1.P$27 (G1), JP1.P$28 (G0), JP1.P$34 (R2), JP1.P$35 (R1), JP1.P$36 (R0), JP1.P$38 (GND3), JP1.P$41 (GND5), JP1.P$42 (GND6), K1.1, K4.1, LED1.-, Q5.2 (E), Q6.2 (E), R6.2, R13.1, R14.2, R21.2, R29.2, R31.1, R44.1, R55.1, R58.1, SD1.6 (VSS), SD1.G1, SD1.G2, SD1.G3, SD1.G4, U1.2 (GND), U2.1 (GND1), U2.40 (GND2), U2.41 (GND3), U2.42 (GND4), U2.43 (GND5), U2.44 (GND6), U2.45 (GND7), U2.46 (GND8), U2.47 (GND9), U2.48 (GND10), U2.49 (GND11), U4.2 (2-GND), U6.1 (GND), U11.7 (GND), U26.2 (GND)
I2S_BCLK: R19.1, U11.3 (BCLK)
I2S_CTRL: R22.1, U11.1 (CTRL)
I2S_SDIN: R4.1, U11.4 (SDATA)
INT: J6.9
IO0_BOOT_CLK: K1.2, Q10.3 (C), R26.1, U2.27 (IO0)
IO1_B7: JP1.P$13 (B7), U2.39 (IO1)
IO2_LCD_BL_CTR: R11.2, U2.38 (IO2), U4.4 (4-EN)
IO3_B4: JP1.P$16 (B4), U2.15 (IO3)
IO4_G7: JP1.P$21 (G7), U2.4 (IO4)
IO5_G2: JP1.P$26 (G2), U2.5 (IO5)
IO6_G3: JP1.P$25 (G3), U2.6 (IO6)
IO7_G4: JP1.P$24 (G4), U2.7 (IO7)
IO8_B3: JP1.P$17 (B3), U2.12 (IO8)
IO9_B6: JP1.P$14 (B6), U2.17 (IO9)
IO10_TF_CS: R67.2, SD1.2 (CS), U2.18 (IO10)
IO11_TF_SPI_MOSI/TP_DIN: R23.2, SD1.3 (DI), U2.19 (IO11)
IO12_TF_CLK/TP_CLK: SD1.5 (SCLK), U2.20 (IO12)
IO13_TF_SPI_MISO/TP_OUT: R24.2, SD1.7 (DO), U2.21 (IO13)
IO14_R7: JP1.P$29 (R7), U2.22 (IO14)
IO15_G5: JP1.P$23 (G5), U2.8 (IO15)
IO16_G6: JP1.P$22 (G6), U2.9 (IO16)
IO17_I2S_SDIN: R4.2, U2.10 (IO17)
IO18_I2S_LRCLK: R12.2, U2.11 (IO18)
IO19_I2C_SDA: J4.7, J6.5, J8.2, R1.1, U2.13 (IO19)
IO20_I2C_SCL: J4.8, J6.3, J8.1, R7.1, U2.14 (IO20)
IO21_R6: JP1.P$30 (R6), U2.23 (IO21)
IO38_D: J2.1, J4.4, U2.31 (IO38)
IO39_HSYNC: JP1.P$9 (HSYNC), U2.32 (IO39)
IO40_DE: JP1.P$7 (DE), U2.33 (IO40)
IO41_VSYNC: JP1.P$8 (VSYNC), U2.34 (IO41)
IO42-I2S_BCLK: R19.2, U2.35 (IO42)
IO45_R3: JP1.P$33 (R3), R31.2, U2.26 (IO45)
IO46_B5: JP1.P$15 (B5), U2.16 (IO46)
IO47_R5: JP1.P$31 (R5), U2.24 (IO47)
IO48_R4: JP1.P$32 (R4), U2.25 (IO48)
LCD_LEDA: C19.2, C21.2, D6.2 (-), JP1.P$39 (LEDA), U4.5 (5-OV)
LCD_LEDK: JP1.P$40 (LEDK), R29.1, U4.3 (3-FB)
LRCLK: R12.1, U11.2 (LRCLK)
unnamed: LED1.+, R3.1
unnamed: C27.2, U11.5 (VON)
unnamed: C14.1, C28.1, J5.P$2
unnamed: JP1.P$10 (DISP), R25.2
unnamed: C28.2, U11.8 (VOP)
unnamed: J3.A5 (CC1), R13.2
unnamed: L4.1, U1.3 (SW)
unnamed: C16.1, C27.1, J5.P$1
unnamed: D6.1 (+), L5.2, U4.1 (1-SW)
unnamed: J3.B5 (CC2), R14.1
unnamed: R20.2, R21.1, U1.5 (FB)
unnamed: Q3.1 (G), R2.1, R44.2
unnamed: R6.1, U26.5 (PROG)
unnamed: Q5.1 (B), R11.1, R58.2
unnamed: Q4.1 (G), Q6.3 (C), R48.2
unnamed: Q9.1 (B), R75.1
unnamed: Q6.1 (B), R54.1, R55.2
unnamed: Q5.3 (C), Q30.1 (G), R172.2
unnamed: Q10.1 (B), R74.1
unnamed: R72.2, U6.2 (TXD)
unnamed: R71.2, U6.3 (RXD)
unnamed: R16.2, SD1.1 (DATA2)
unnamed: R17.2, SD1.8 (DATA1)
RTS: Q9.2 (E), R74.2, U6.14 (RTS#)
TFT-3V3: C3.1, C10.2, C15.2, C23.2, JP1.P$37 (VCC), Q4.3 (D), R25.1, R56.2
TP_RST: J6.7, R5.2
TP_X+: JP1.P$4 (XR)
TP_X-: JP1.P$2 (XL)
TP_Y+: JP1.P$3 (YD)
TP_Y-: JP1.P$1 (YU)
UART0_RXD0: J10.1, R72.1, U2.36 (RXD0)
UART0_TXD0: J10.2, R71.1, U2.37 (TXD0)
USB_D+: R9.2, U6.5 (UD+)
USB_D-: R8.2, U6.6 (UD-)
VBUS: C49.2, C50.1, D3.1 (+), J3.A4 (VBUS), J3.A9 (VBUS), J3.B4 (VBUS), J3.B9 (VBUS), R2.2, U26.4 (VCC)
VDD: C24.1, C25.1, R10.2, R45.2, U11.6 (VDD)
VIN: C6.2, C42.2, D3.2 (-), D5.C, Q3.2 (S), Q30.2 (S), R45.1, R172.1, U1.1 (EN), U1.4 (VIN)
VIN2: C18.2, C43.2, L5.1, Q30.3 (D), U4.6 (6-VIN)

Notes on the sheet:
Vout=0.6*(R20/R21 +1)=3.3V
sys 3.3V power
UART0 port
ESP32-S3-WROOM-1-N4R8
USB type-c socket
battery
IO0 low lv:download high lv:enable SPI
EN high lv:enable IC low lv:disable IC
USB to serial
IIS NS4168
TF Card
BOOT
RESET
POWER LED
LCD+TP interface
Vout=0.6*(1+RU/RN)
D port
500mA
BAT

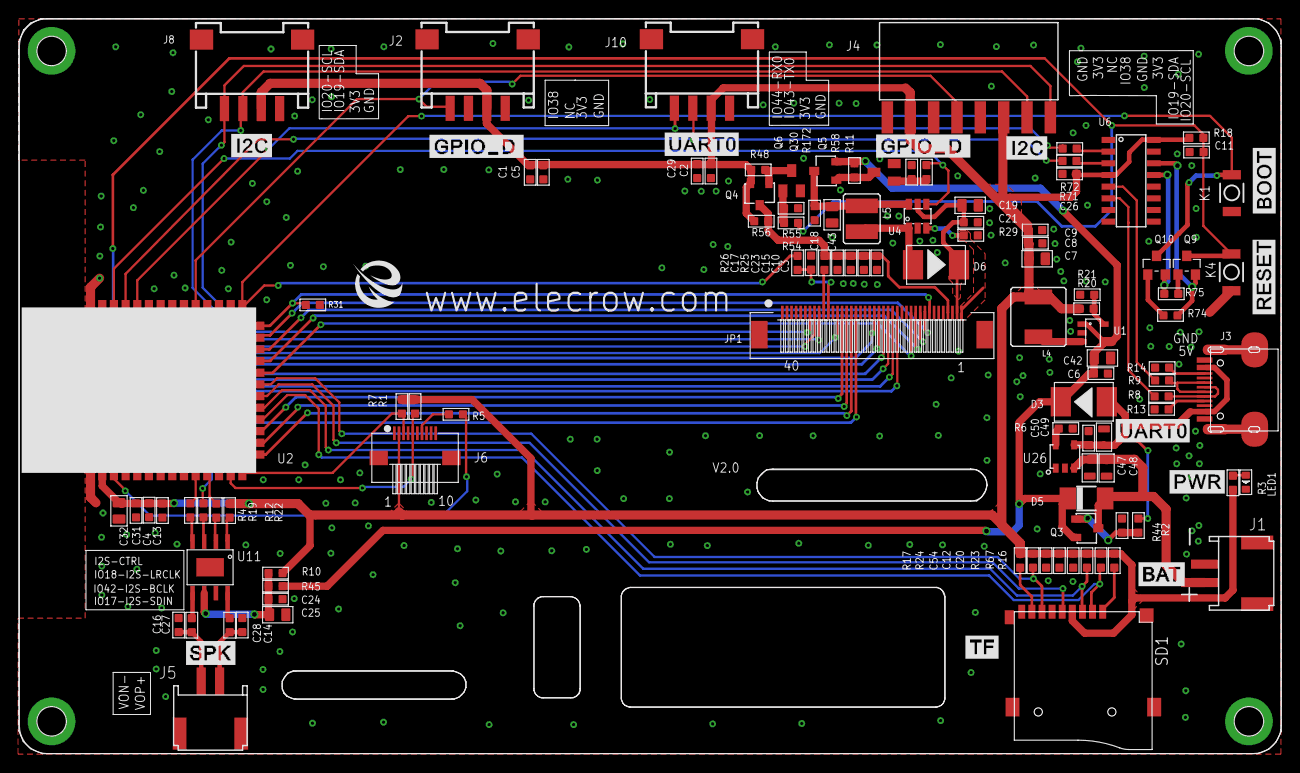
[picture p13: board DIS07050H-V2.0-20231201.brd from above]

Board: 2 copper layers, 137.3 x 79.9 mm, 111 parts (1 on the bottom side), 79 nets.

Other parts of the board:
U$30: ELECROW-NEW
U$33: 5.0底框
U$41: 5.0板框

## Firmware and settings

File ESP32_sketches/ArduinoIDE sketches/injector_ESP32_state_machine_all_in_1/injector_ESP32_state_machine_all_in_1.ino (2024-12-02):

// injector_ESP32_state_machine.ino

/* sketch to control motorized injection machine via ESP32 for direct Nema34 160mm with external DM860H
driver, 3 inductive endstops, 3 lower keypad buttons with Neopixel LEDs behind them to indicate distinct
funtionality, SPI thermocouple, & independant Encoder to Motor comparison, all via a State Machine to 
progress thru different machine states, using either sensor or user input via buttons

sketch should return via Serial data on Encoder and Temp, later this ESP32 will be connected via UART to 
a ESP32 Display, which will hold different mould structs, and therefore be able to load to the motor ESP32
distinct injection parameters as per mould to inject, and also keep track from Encoder data of when the 
injector is Refilled, so each Refill will be graphically represented by a rectangule inside a tube like 
graphic, move down and change color as injection and refills happens, & have a timing tracker to be able 
to see if it has had enough time to melt (avoiding cold injections!) */




/* global varible definitions & declaractions, some may be moved to local funtions, but 
leave here and comment out where they have gone - QUESTION: can LOCAL variables within functions be changed via 
serial message updates..? ex: compressionFunction has local speedReductionFactor & comparisonPercentage, during 
initial sketch & machine calibration, it may be necessary to update these values, would be easier via Serial
than flashing...? Although in theory, once checked and sure cannot cause infinite loop, should again be purely 
local and never need changing
 */

// pin definitions, decided on from "GPIO_Limitations_ESP32_NodeMCU.jpg", and which side may be more convenient

#define UART_tx_ESP32 17                         // * TX2 UART comms with ESP32
#define UART_rx_ESP32 16                         // *
#define ENCODERApin 36                           // * A+ encoder pin, A- not used  "CLK ENCODER "
#define ENCODERBpin 39                           // * B+ encoder pin, B- not used  "DT ENCODER "
#define StepperSTEPPin 32                        // * any GPIO for ESP32
#define StepperDIRPin 33                         // * may not be needed if using -ve moves..?
#define EndstopTOPPlungerPin 22                     // * all buttons/endstops with INPUT_PULLUP to avoid floating values
#define EndstopBOTTOMPlungerPin 21                  // * so all ACTIVE STATES are ==0
#define EndstopBARRELClampOKPin 5                   // *
#define EndstopMOULDPresentPin 12                   // do not yet have a way of detecting, possibly pressure sensor under plastic floor on platform..?
#define EndstopNOZZLEBlockForCompressOrPurgePin 15  // also as above, not decided hardware method yet
#define TEMPNozzleVSPI_MISO_DO MISO              // * 19
#define TEMPNozzleVSPI_Dpin_MOSI_CS MOSI         // * 23 these 3 pins are for daughter PCB thermocouple
#define TEMPNozzleVSPI_SCK_CLK SCK               //  *  18 (possible change to analog component if run out of pins
#define BUTTONDownPin 26                         // * these 3 pins for lower keypad, to facilite Purge and INject Confirm
#define BUTTONUpPin 27                           // *
#define BUTTONSelectPin 14                       // *
#define WS2812B_ButtonAddressableLEDsPin 25         // * 1 pin to address 3 LEDs buttons...
#define WS2812B_RingAddressableLEDsPin  2            // 1 pin for 35 LEDs nozzle ring, to change color as per moment of use..
#define EMERGENCYStopPin 4                           //  *
//#define CURRENTSensor1   34      // * as yet to be decided on how to use motor phase current readng
//#define CURRENTSensor2   35      // * to be useful for detecting motor current (reaching amc compression/fill)

//////////////////////////////////

// global constants
// revise what is now NOT NEEDED, OR what variables should go inside Functions to make LOCAL

/* global common variables for machine limits and moves to offsets, these, once identified the max values
should NEVER need changing, even from advanced Common panel, as superior values run the risk of machine
performing outside of the decided security limits of movement/accel, distances, etc
revise what is  NOT NEEDED, OR what variables should go inside Functions to make LOCAL*/
const int minTempForAnyMove = 170;              // min temp considered safe for machine move
const int maxSpeedLimit = 2000;                 // 2000 corresponds to 5rps NEMA, about 1/4 rps gear, about 18.85/4 = 4.7125cm linear
                                                // plunger movement, about 25cm3 injected volume, per second MAX speed limited
const int moveContinuosDistSteps = 5000;        // arbitrary large distance for continuous movements, gets reset to 0 each loop anyway
const int defaultAcceletationNema = 50000;      /* check in reality, maybe large moulds will benefit from slower acceleration together with higher speeds..?
                                            to avoid blocking motor/losing steps with high speed requests with too high accelerrations..
                                           or smaller moulds benefit also from slower acceleration/speed so as not to explode, or fill with
                                           less acceleration tapering off... */
const int maxHomingStepsDistSteps = 30000;      // CHECK THIS NUMBER OF STEPS COVERS WHOLE MOVEMENT RANGE, HEATED ZONE + REFILL + TOPENDSTOP + extra
const int totalStrokeStepsDistSteps = 21220;    //calc'd value, check against real, this is ONLY HEATED ZONE, need another OFFSET from Encoder 0
const int refillOpeningOffsetDistSteps = 3800;  // ESTIMATED! once homed to top endstop, how far to move to position just above filling hole in barrel
                                                // THIS VALUE HAS TO BE FOUND BY CALIBRATION AND ADJUSTED TO REALITY!!
const int heatedZoneOffsetDistSteps = 7200;     // calc'd value, check with reality
const int buttonShortPress = 500;               // for short press of button, ms
const int buttonLongPress = 2000;               // long press...
const int debounceInterval = 5;


// for motor Funtion, to be re-written depenging on State to these variables
int motorSpeed;         // example, for INJECT state, motorSpeed=FillMouldMoveSpeed, then call ProgrammedMotorMove
                        // should use this updated value for this next call of ProgrammedMotorMove
int motorAcceleration;  // same as above, requires each State that contemplates using ProgrammedMotorMove
                        // to have all three values, otherwise risk of using older value from previous call!
int motorMove;          // same as above, is a RELATIVE move (not moveTo!)
int MotorDir;           // direction of ANY motor move, or can this be omitted as DistSteps variables can be -ve..?
int MotorPosition;      /* reference position for next ProgrammedMotorMove, set to 0 after Purge is finished... possibly 
                        not needed as all moves should be RELATIVE, and resetting motor position does not need a variable */
int stepsMoved = 0;     // Track the number of steps moved, to compare to steps made, and also for encoder comparison
/* steps to cm3 & cml conversion 
volumen    80steps = 1cm3,  2000steps = 25cm3  (average 2D mould approx)
linear    424steps = 1cml, 21220steps = 50cml  (total useful heating zone, below Refill offset)
*/
int stepsToCM3 = 80;
int stepsToCML = 424;


/* global common variables, different types of movement parameter storage, to be sent from ESP32 or stored 
locally as common constants between all injection/homing/compression/ etc processes..
during initial calibration of machine, will refine these values, probably from advanced access
panel on display, that will later be fixed (or advanced panel will be hidden from user until
certain combo of button presses will reveal, but these common values should not need changing
once initial machien calibration has found ideal values)
FIND IDEAL VALUES OF THESE COMMON PARAMETERS AND INITIALIZE HERE!! Could become constants, but should be changable 
under certain (testing & calibration?) purposes
*/
char StatesMachine;
char runState;  // states for movement functions (purge, inject, etc), 0 to ensure when no button is pressed, no movement
// int readyState=0  // states for non-moving ready states  - N/A
long int PurgeSpeed = 80;                   // speed for purge move, continous move until button release  80= 1cm3/s
long int GeneralFastSpeed = maxSpeedLimit;  // how fast to home, continous move until reaching endstop, also for other general moves..? max /2..?
// homing params moved to Homng Function as not needed elsewhere
// int HomingDirection;      // maybe not needed, as maxHomingStepsDistSteps can be -ve..?
// int HomeOffSetDistSteps;       // once first reached HomeEndstop, how much to back off before slower approach
// int HomeOffSetAccel;      // once first reached HomeEndstop, how much Accel to back off before slower approach
// int HomeOffsetSpeed;      // once first reached HomeEndstop, how quic to back off before slower approach
// int HomingSlowSpeed;      // how slow to home, 2nd approach, continous move until reaching endstop
long int initialCompressionSpeed = GeneralFastSpeed / 2;                    // could be GeneralFastSpeed / 2..?
long int minCompressionSpeed = GeneralFastSpeed / 20;                       // at what speed is compression no longer useful..?
long int comparisonPercentage = 50;                                         /* EXAMPLE VALUE what % difference between sent motor steps and read encoder steps should a change 
                            in speed be commanded?
                            higher % will cuase more skipping before changing speed, lower % will cause more speed changes (o vica versa),
                            but also possibly increase probability of infinite loop, if use line comparisonPercentage *= speedReductionFactor; */
long int speedReductionFactor = 5;                                          // EXAMPLE VALUE Percentage to reduce speed when comparisonPercentage limit reached
long int AntiDripReverseTime = 15000;                                       // 15s in case if using ConstMotorMove, instead of ProgrammedMotorMove, how many seconds before cancel..?
long int AntiDripReverseSpeed = stepsToCML / (AntiDripReverseTime / 1000);  // 80steps/15, per sec.. after purge, to recuperate and avoid drip until mould is placed - TEST
long int AntiDripReverseMillis;                                             //  after purge, start millis timer
// using distance: normally the user SHOULD press INJECT button BEFORE this move is completed, but if is ProgrammedMotorMove,
// can I interrupt this move before it completes..?
long int AntiDripFinalOffset;                    // once AntiDrip constMoveBack is interrupted with button press for injection, store actual motor position and sum to 0?
long int ReleaseMouldMoveSpeed = maxSpeedLimit;  // after hold, must raise the barrel a few mm to free mould for removal.. most likely will be a constant
long int ReleaseMouldMoveDistSteps = -200;       //  same as above, 200 steps is approx 0.47cm, -ve as ProgMotorMove is normally +ve downward
long int constantInjectionParams[] = {
  PurgeSpeed,
  GeneralFastSpeed,
  initialCompressionSpeed,
  minCompressionSpeed,
  comparisonPercentage,
  speedReductionFactor,
  AntiDripReverseTime,
  AntiDripReverseSpeed,
  ReleaseMouldMoveSpeed,
  ReleaseMouldMoveDistSteps
};

/* array to hold message with above constant parameters, to be assigned to and returned to ESP32..?
 ={PurgeSpeed, GeneralFastSpeed, initialCompressionSpeed, AntiDripReverseSpeed, AntiDripReverseDistSteps, ReleaseMouldMoveSpeed, ReleaseMouldMoveDistSteps}
*/

/* actual injection variables, will be adjusted each time for each different mould, user will have access
via panel on display to change these values whilst calibrating a mould, and will then be stored on Display
ESP32 in Flash as array/struct of values particular to each mould
*/
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
  void loop() {
    CheckMinTempEndstopsEmergencyStopPin();
    MachineState(int runState);
  }

/*
  // functions declarations, to try and organize most commonly re-used functions
  long EncoderActualPosition();                                             // reads encoder position and returns REFERENCE variable for use by other functions
  void ResetEncoderZero();                                                 // resets Encoder to Zero, ONLY to be called ONCE at power up, toggle initialHomingDone
  void ProgrammedMotorMove(motorSpeed, motorAcceleration, motorMove);      // simply moves motor at set speed, accel and distance indicated
  void ContinuousMotorMoveForward(motorSpeed);                             // simply moves plunger continously (during button press or other condition is 0/1)
  void ContinuousMotorMoveBackward(motorSpeed);                            // simply moves plunger continously (during button press or other condition is 0/1)
  void HomeMove(GeneralFastSpeed, HomingSlowSpeed);                                 // simply sends plunger to TopEndstop - CAN USE ContinuousMotorMoveBackward
  bool compareMotorEncoder();                                              // function to compare Encoder & FastAccel position, to detect when skipping steps, 
and therefore compression of plastic or filling of mould, and to reduce speed/distance commands until are below min threshold,
when then returns "complete"/"1" to function where has been called from 
  void compressionFunction(initialCompressionSpeed, minCompressionSpeed);  // ChatGPT written compression uses compareMotorEncoder funtion
  void clearLEDs();                                                        // clears LEDs and turns off, before next colour setting
  void ButtonLEDsColors(selectLEDcolour, upLEDcolour, downLEDcolour);      // sets colours of LEDs behind buttons
  void SerialRegular100msMessages();                                       // every 100ms, send via serial the Temp, Encoder position, etc
  void SerialChangeOfState();                                              // serial print when a change of state happens, and new state
  void SerialPrintNextInjectionValues();                                   // serial print the parameters of next injection
  void BounceButtonsSetup();                                               // setup of buttons list to avoid setup() overload
  void BounceButtonsUpdateCall();                                          // same for button update call in loop()
  int CheckMinTempEndstopsEmergencyStopPin();                                // should run in each loop, and if any endstop or emergency stop is triggered, stop machine 
and report which endstop has been triggered... possible thereafter only allow moves in opposite direction, or back to refill, or 
other options..? */

  //////////////////////////////////

  // functions fully described

  // Encoder function will get called not every loop, but maybe every 10ms, to give time for max distances to trigger other code, and every 100ms
  // wil be called by SerialRegular100msMessages, where if motor is stopped, actual = old, and no need to print value
  long EncoderActualPosition() {
    actualENPosition = encoder.getCount() / 2;  // revise last int, if motor steps = 400 & encoder PPR = 1000, adjust this int
                                                // (possible issue of needing to round, this is bad, better maybe to increase driver steps to same as encoder?)
    oldENPosition = actualENPosition;           // if this does NOT change between Serial.prints, then don't print

    return (actualENPosition);
  }

  void ResetEncoderZero() {
    encoder.clearCount();

    return;
  }

  // motor functions
  /* NOTE: When calling this function from different states, it will be called with the arguments particular to that state, ex.
INJECT will pass ProgrammedMotorMove(FillMouldMoveSpeed, FillMouldAccel, FillMouldMoveDistSteps)... will this AUTOMATICALLY write those 
parameters to the functions named paramters, ie motorSpeed, motorAcceleration, motorMove..? Because if I wish to do a later
compareMotorEncoder function, this function needs to have the ProgrammedMotorMove NAMED params, not the PASSED params names..?
 */
  void ProgrammedMotorMove(motorSpeed, motorAcceleration, motorMove)  // RELATIVE motor move to new position
  {
    stepper->setSpeedInHz(motorSpeed);
    stepper->setAcceleration(motorAcceleration);
    stepper->move(motorMove);
  }


  void ContinuousMotorMoveForward(motorSpeed)  // CONTINUOUS motor move IF/WHILE a condition is met (button press, !endStop trigger, etc)
  {
    stepper->setSpeedInHz(motorSpeed);
    stepper->runForward();
  }

  void ContinuousMotorMoveBackward(motorSpeed)  // CONTINUOUS motor move IF/WHILE a condition is met (button press, !endStop trigger, etc)
  {
    stepper->setSpeedInHz(motorSpeed);
    stepper->runBackward();
  }

  int HomingSlowSpeed = maxSpeedLimit / 10;  // how slow to home, 2nd approach, continous move until reaching endstop
  void HomeMove(GeneralFastSpeed, HomingSlowSpeed)  // once called, no user action can stop until complete!
  {
    //int HomingDirection;      // maybe not needed, as using ContMoveBackwards
    int HomeOffSetDistSteps = 212;             // once first reached HomeEndstop, how much to back off before slower approach, 212 steps ≈ 5mm
    int HomeOffSetAccel = 10000;               // once first reached HomeEndstop, how much Accel to back off before slower approach 10000 = 1/5th normal
    int HomeOffsetSpeed = maxSpeedLimit / 2;   // once first reached HomeEndstop, how quick to back off before slower approach
    int HomingSlowSpeed = maxSpeedLimit / 10;  // how slow to home, 2nd approach, continous move until reaching endstop
    if (digitalRead(EndstopTOPPlungerPin) == !topPlungerEndstopActive) {
      ContinuousMotorMoveBackward(GeneralFastSpeed);  // OR ProgrammedMotorMove with maxHomingStepsDistSteps, if fails, gives error?
    }
    ProgrammedMotorMove(HomeOffsetSpeed, HomeOffSetAccel, HomeOffSetDistSteps);  // programmed motor move assumed to be positive DistSteps..?
    if (digitalRead(EndstopTOPPlungerPin) == !topPlungerEndstopActive) {
      ContinuousMotorMoveBackward(HomingSlowSpeed);
    }
  }

  // function to compare Motor & Encoder positions
  bool compareMotorEncoder(motorMove, actualENPosition, comparisonPercentage)  // chatGPT written
  {
    // Calculate difference between motor position and encoder position
    int motorError = abs(motorMove - actualENPosition);

    // Calculate the acceptable difference threshold
    int threshold = (motorMove * comparisonPercentage) / 100;

    // Return true if the difference is greater than the threshold
    return (motorError >= threshold);
  }

  /* motor compression function takes compareMotorEncoder and motor moves to apply pressure up to a threshold and then
reduce the speed (increases torque of stepper?) until again threshold past, etc, until minCompressionSpeed reached, thenwill stop */
  void compressionFunction(initialCompressionSpeed, minCompressionSpeed)  // chatGPT written
  {
    ButtonLEDsColors(, BLACK_rgb, );
    select_button.update();

    // add ButtonSelect interrupt function on user press, goes to Ready_to_Inject (also EStop..? or EStop better permament in loop
    //  and then goes to ERROR-STATE?)
    if (!select_button.isPressed) {
      // Set initial speed
      stepper->setSpeedInHz(initialCompressionSpeed);  // Starting speed in steps per second

      while (stepper->getSpeed() > minCompressionSpeed) {
        // Move the plunger down
        stepper->runForward();

        // Call the comparison function to check if motor-encoder difference exceeds threshold
        if (compareMotorEncoder(stepper->getTargetPosition(), encoder.getPosition(), comparisonPercentage)) {
          // Reduce speed when the difference is greater than the allowed threshold
          int newSpeed = stepper->getSpeed() * (speedReductionFactor / 10);
          stepper->setSpeedInHz(newSpeed);
          ButtonLEDsColors(, BLACK_rgb, YELLOW_rgb);  // to show compression is acting (has reduced speed at least once) and ongoing..

          // Optionally, reduce comparison threshold on each iteration (for finer control)
          comparisonPercentage *= speedReductionFactor; /* could lead to infinite smaller steps if minCompressionSpeed is too low...? 
          for debugging this option, would be good to show actual speed - if later wish to add another compressionDuringHeating function
          where the plastic is already quite compressed, and will start (and end) from/to a much lower speeds, have to make sure this 
          does not produce infinite loop as never reaches minCompressionSpeed */
        }
      }
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

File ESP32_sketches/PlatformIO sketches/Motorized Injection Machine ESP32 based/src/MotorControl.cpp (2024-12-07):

#include "MotorControl.h"
#include "globals.h"

FastAccelStepperEngine engine = FastAccelStepperEngine();
FastAccelStepper *stepper  = NULL;

void initMotor()
{
    engine.init(0);     // core assignment
    #if defined(SUPPORT_SELECT_DRIVER_TYPE)
    stepper = engine.stepperConnectToPin(STEPPER_STEP_PIN,1);
    #endif
    if (stepper)
    {
        stepper->setDirectionPin(STEPPER_DIR_PIN);
        stepper->setAcceleration(50000);
    }
}

void ProgrammedMotorMove(int motorSpeed, int motorMoveSteps, unsigned int motorAcceleration=50000) // simply moves motor at set speed, accel and distance indicated
// This would allow for simpler calls where acceleration doesn't change: ProgrammedMotorMove(1000, 2000); // Speed and steps only
//                                                                 ProgrammedMotorMove(1000, 2000, 60000); // Full control
{
    if (stepper)
    {
        stepper->setSpeedInHz(motorSpeed);          // speed in Hz = steps/s
        stepper->move(motorMoveSteps);
        stepper->setAcceleration(motorAcceleration);
    }
}

void ContinuousMotorMoveForward(int motorSpeed) // CONTINUOUS motor move IF/WHILE a condition is met (button press, !endStop trigger, etc)
{
    if (stepper)
    {
        stepper->setSpeedInHz(motorSpeed);
        stepper->runForward();
    }
}
    
void ContinuousMotorMoveBackward(int motorSpeed) // CONTINUOUS motor move IF/WHILE a condition is met (button press, !endStop trigger, etc)
{
    if (stepper)
    {
        stepper->setSpeedInHz(motorSpeed);
        stepper->runBackward();
    }
}


void stopMotor()
{
    if (stepper)
    {
        stepper->stopMove();
    }
}

void setMotorSpeed(int motorSpeed)
{
    if (stepper)
    {
        stepper->setSpeedInHz(motorSpeed);
    }
}

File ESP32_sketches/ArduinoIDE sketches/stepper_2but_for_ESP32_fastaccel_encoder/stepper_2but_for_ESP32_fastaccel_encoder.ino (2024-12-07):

/*   
stepper_2but_for_ESP32_fastaccel_encoder.ino
 */
 
#include "globals.h"

#include <RotaryEncoderPCNT.h>
#include <FastAccelStepper.h>
#include <elapsedMillis.h>
#include <Adafruit_NeoPixel.h>
#include <Bounce2.h>



RotaryEncoderPCNT encoder(CLK, DT);


FastAccelStepperEngine engine = FastAccelStepperEngine();
FastAccelStepper *stepper = NULL;

elapsedMillis printTime;

Adafruit_NeoPixel keypadleds (KEYS_LED_COUNT, KEYS_LED_PIN, NEO_GRB + NEO_KHZ800);

// INSTANTIATE A Button OBJECT FROM THE Bounce2 NAMESPACE
Bounce2::Button TOP_ENDSTOP = Bounce2::Button();
Bounce2::Button BOTTOM_ENDSTOP = Bounce2::Button();
Bounce2::Button BARREL_ENDSTOP = Bounce2::Button();
Bounce2::Button EMERGENCY_STOP = Bounce2::Button();
  /* ADJUST & ADD BUTTON PIN READS TO USE BOUNCE2 LIBRARY, as in bounce_inductive_tests_to_LEDs.ino */



void setup() 
{
  Serial.begin(115200);
  pinMode(downPin, INPUT_PULLUP);
  pinMode(upPin, INPUT_PULLUP);

old_position = encoder.position();
//Serial.println(old_position);


  engine.init();     // core assignment to 0..?  /* this causes panic messages and ESP sends errors
 //#if defined(SUPPORT_SELECT_DRIVER_TYPE)
    stepper = engine.stepperConnectToPin(stepPinStepper);  // convert to DRIVER 1, RMT
  //  #endif   /* this causes not to compile when included 2nd argument for RMT DRIVER */
 
  if (stepper) 
  {
    stepper->setDirectionPin(dirPinStepper);
    //stepper->setSpeedInHz(runSpeed);  // the parameter is Hz, steps/s !!!
    stepper->setAcceleration(motor_def_accel);
    //stepper->move(moveDist);
  }

  keypads_setup();
  bounce2_buttons_setup();

}

void keypads_setup()
{
  keypadleds.begin();            // Call this to start up the LED strip.
                                 //  clearLEDs();   // This function, defined below, turns all LEDs off...
  keypadleds.setBrightness(50);  // Set BRIGHTNESS to about 1/5 (max = 255)
  keypadleds.show();             // ...but the LEDs don't actually update until you call this.
}

void bounce2_buttons_setup() 
{
    /* ADJUST & ADD KEYPAD BUTTONs TO USE BOUNCE2 LIBRARY, as in bounce_inductive_tests_to_LEDs.ino */

  // SELECT ONE OF THE FOLLOWING :
  // 1) IF YOUR BUTTON HAS AN INTERNAL PULL-UP or PULL-DOWN
  TOP_ENDSTOP.attach(TOP_ENDSTOP_PIN, INPUT_PULLUP);
  BOTTOM_ENDSTOP.attach(BOTTOM_ENDSTOP_PIN, INPUT_PULLUP);    //Top & Bottom NO, 5v
  BARREL_ENDSTOP.attach(BARREL_ENDSTOP_PIN, INPUT_PULLDOWN);  //FINDA sensor is NC, 0v
  EMERGENCY_STOP.attach(EMERGENCY_STOP_PIN, INPUT_PULLUP);    // CHECK THAT IS NO!!

  // DEBOUNCE INTERVAL IN MILLISECONDS
  TOP_ENDSTOP.interval(DEBOUNCE_INTERVAL);
  BOTTOM_ENDSTOP.interval(DEBOUNCE_INTERVAL);
  BARREL_ENDSTOP.interval(DEBOUNCE_INTERVAL);
  EMERGENCY_STOP.interval(DEBOUNCE_INTERVAL);

  // INDICATE THAT THE LOW STATE CORRESPONDS TO PHYSICALLY PRESSING THE BUTTON
  TOP_ENDSTOP.setPressedState(LOW);  // NO, with pullup, goes LOW when closed
  BOTTOM_ENDSTOP.setPressedState(LOW);
  BARREL_ENDSTOP.setPressedState(HIGH);  //  NC, with pulldown, goes HIGH when active
  EMERGENCY_STOP.setPressedState(LOW);   //  CHECK THAT IS NO!!
}

void executeMotorCommand(int8_t runState)
{
  switch (runState)
  {
    case 0:
//	  stepper1.setAcceleration(200);
      stepper->stopMove();
	    motorSpeed = 0;
	    //stepper->setCurrentPosition(0);
      break;
    case 1:
	    stepper->setSpeedInHz(runSpeed);
	    stepper->runForward();
      break;
    case -1:
	    stepper->setSpeedInHz(runSpeed);
	    stepper->runBackward();
      break;
  }
}

void PrintData()
{
  if ((printTime >= 200))
   {
    Serial.print("Down: ");
    Serial.print(downPinState);
    Serial.print(", Up: ");
    Serial.print(upPinState);
    Serial.print(", rS: ");
    Serial.print(runState);
    Serial.print(", Sp: ");
    Serial.print(runSpeed);
    Serial.print(", En: ");
    Serial.print(position);
    Serial.print(", FAS: ");
    Serial.println(stepper->getCurrentPosition());
   /* Serial.print(" ");
    Serial.print("D");
    Serial.print(" ");
    Serial.println(stepper1.distanceToGo());*/
    printTime=0;
   }
}


void loop() 
{
  position = encoder.position()/10;
    // UPDATE THE BUTTON
  // YOU MUST CALL THIS EVERY LOOP
  BARREL_ENDSTOP.update();
  TOP_ENDSTOP.update();
  BOTTOM_ENDSTOP.update();
  EMERGENCY_STOP.update();
  /* ADJUST PIN READS TO USE BOUNCE2 LIBRARY, as in bounce_inductive_tests_to_LEDs.ino */


  downPinState = digitalRead(downPin);
  upPinState = digitalRead(upPin);

  if ((downPinState == 0 && upPinState == 0) || (downPinState == 1 && upPinState == 1)) 
  {
    runState = 0;
    executeMotorCommand(runState);
  }
  else if (downPinState == 0 && upPinState == 1)
  {
    runState = 1;
    executeMotorCommand(runState);
  }
  else if (downPinState == 1 && upPinState == 0)
  {
    runState = -1;
    executeMotorCommand(runState);
  }

  motorSpeed =  map(potReading, 0, 1023, 5, maxSpeedLimit);
  runSpeed = (motorSpeed); 

  PrintData();
}

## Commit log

2024-11-05 Add files via upload
    added photos of electrical backboard layout (slight changes since photo), LLC setup, manuals for driver, LLC, and Nema Motor, and ESP32 pinout choices
2024-12-02 added more docs
    [DIS07050H-V2.0-20231201.brd, DIS07050H-V2.0-20231201.sch]
2024-12-02 added ESP32 code tests
    [calcs new injector.xlsx]
2024-12-02 new test sketches via ArduinoIDE OK
2024-12-07 flow & no-flow examples
2024-12-31 tocado por Roberto, quien sabe que puede haber pasado!
2025-01-29 fix folder name
    [DIS07050H-V2.0-20231201.brd, DIS07050H-V2.0-20231201.sch]
2025-01-30 Rename reversable nozzle: barrel blocking mech, blocks nozzle during compression, blocks barrel only during Purge.png to reversable nozzle barrel blocking mech, blocks nozzle during compression, bloc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

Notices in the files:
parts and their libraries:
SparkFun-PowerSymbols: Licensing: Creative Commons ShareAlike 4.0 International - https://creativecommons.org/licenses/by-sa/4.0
